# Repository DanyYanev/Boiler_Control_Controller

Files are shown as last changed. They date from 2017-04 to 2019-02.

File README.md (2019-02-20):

# Boiler_Control_Controller

## Awards

Business choice award from <b>TelebidPro</b> at <b>TUES FEST</b>

## Assignment 
 
Developing an easy-to-use device for controlling complicated water-heating systems through relays, giving the end user the ability to easily manage the heating system by the provided local touchscreen display, or remotely done so by the developed mobile Android application.

## General Characteristics of the problem

The product allows the end-user to easily and quickly control the system while being very efficient on resources such as time, electricity and water and taking fault proof into consideration.
It’s especially useful when manging the heating system of a distanced house in an underpopulated location. Using this system frees you from the responsibility to go there and manually manage everything and allows you to quickly setup your heating system just in time before you arrive as if you were just there yesterday. 

## General Working Schema

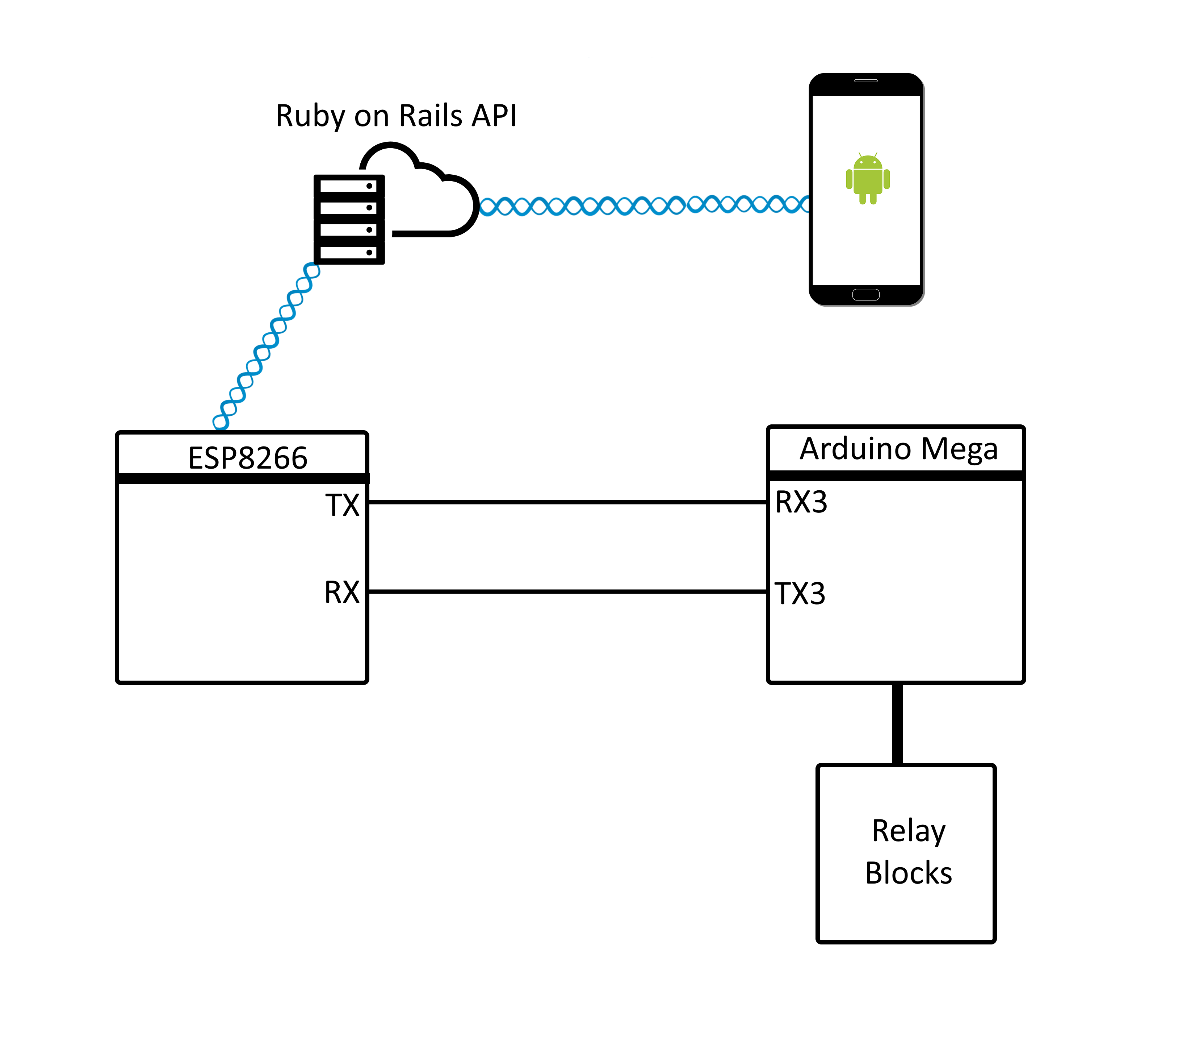
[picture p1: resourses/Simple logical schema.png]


  The whole system water-heating system is controlled by an Arduino Mega that communicates with an ESP8266 Module, the GUI is a [Nextion Display](https://nextion.itead.cc/) which is getting programmed through the Nextion Editor. All pictures were designed using Adobe Photoshop and are located in [here](/resourses/pictures/).

  The Arduino Mega and the ESP module communicate through regular serial. The serialEvent interrupt function in each controller parses the messages.

  The main functionality of the ESP module is to communicate with the API via HTTP requests. While the Mega is responsible for building the logic and managing the hardware. Both devises have acknowledgement whether or not a message has been parsed successfully.
		
  Every 10 seconds the ESP module attempts to fetch information from the server via a GET request at “[server_ulr]/users/[user_token]”. Every device has a unique user-generated user token and a controller token which is built in the ESP module and is unique for every microcontroller. After a successful request the body of the request is fetched and sent to the Mega controller. The body contains a JSON specified by the API Documentation here. If the parsing is successful the Mega controller will send an acknowledgement message. 

The ESP won’t send data to be parsed if the current running configuration is the same as the one fetched from the server.

After a local change is made the Mega will prepare a new JSON with the changes.

  Every 5 seconds if a change is made to the configuration, the updated JSON will be parsed to the ESP which will then wrap it in a PUT request and send it to the server. If an update is successful an acknowledgement message will be sent to the MEGA and the JSON object will be flushed. Else the MEGA will continue to send the updates every 5 seconds.

  All required variables for the logic to be built are saved in EEPROM. In case of power loss, on startup all variables are loaded from the local non-volatile memory.

Controller code for Boiler_Control project. ELSYS-2018

App Repo - https://github.com/DanyYanev/Boiler_Control_App

Server Repo - https://github.com/DanyYanev/Boiler_Control_Server

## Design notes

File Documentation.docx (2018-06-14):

ТЕХНОЛОГИЧНО УЧИЛИЩЕ ЕЛЕКТРОННИ СИСТЕМИ към ТЕХНИЧЕСКИ УНИВЕРСИТЕТ - СОФИЯ

# К У Р С О В П Р О Е К Т

Тема: Проектиране и реализация на контролер за отоплителна система

с GUI и Remote Access

Ученици: Даниел Янев | Научен ръководител: Инж. Росен Витанов
Денис Христов Виктор Найчев | М. Инж. Кирил Митов

СОФИЯ

2018

Assignment:

Developing an easy-to-use device for controlling complicated water-heating systems through relays, giving the end user the ability to easily manage the heating system by the provided local touchscreen display, or remotely done so by the developed mobile Android application.

GENERAL CHARACTERISTICS OF THE PROBLEM

The product allows the end-user to easily and quickly control the system while being very efficient on resources such as time, electricity and water and taking fault proof into consideration.

It’s especially useful when manging the heating system of a distanced house in an underpopulated location. Using this system frees you from the responsibility to go there and manually manage everything and allows you to quickly setup your heating system just in time before you arrive as if you were just there yesterday.

# Chapter I. Function Call Tree, Shield, Modularity, Principal Heating Schema, Memory Management, Controller communication, Libraries.

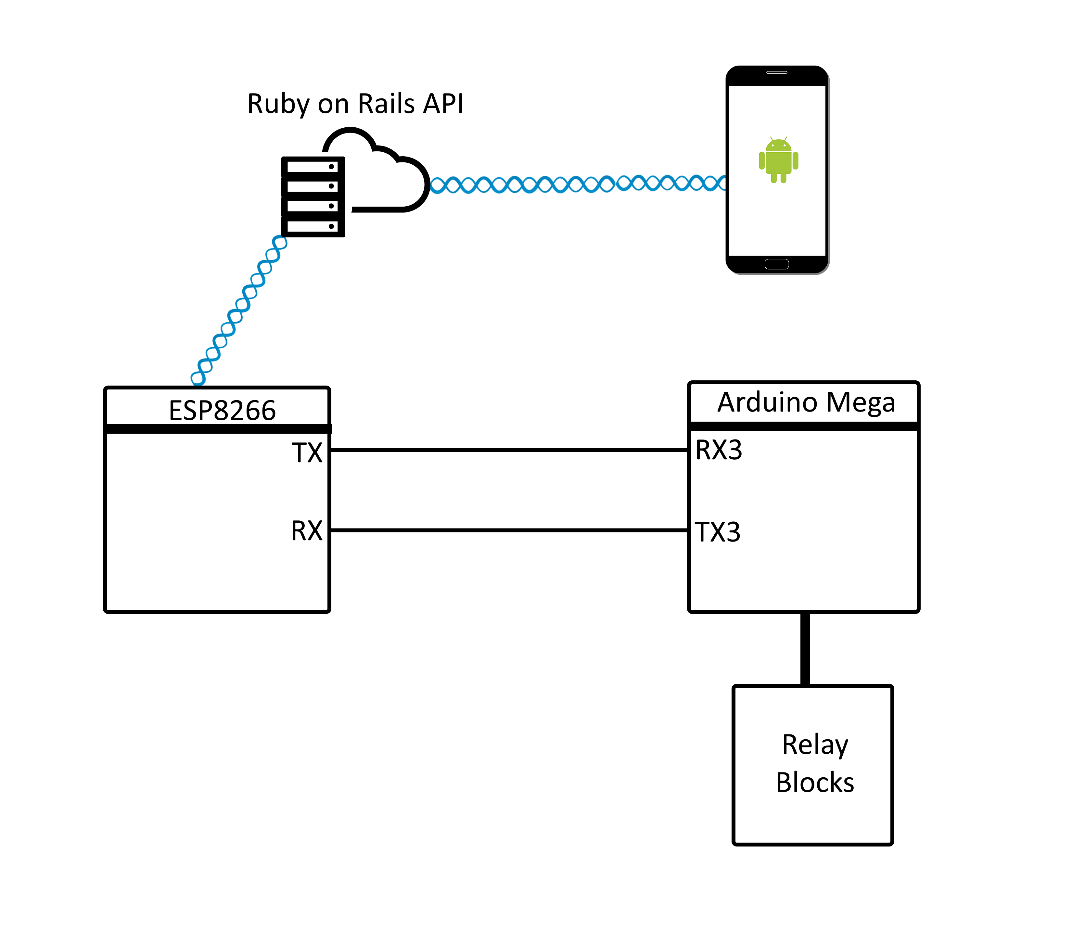
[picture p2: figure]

1. Simple Logical Scheme

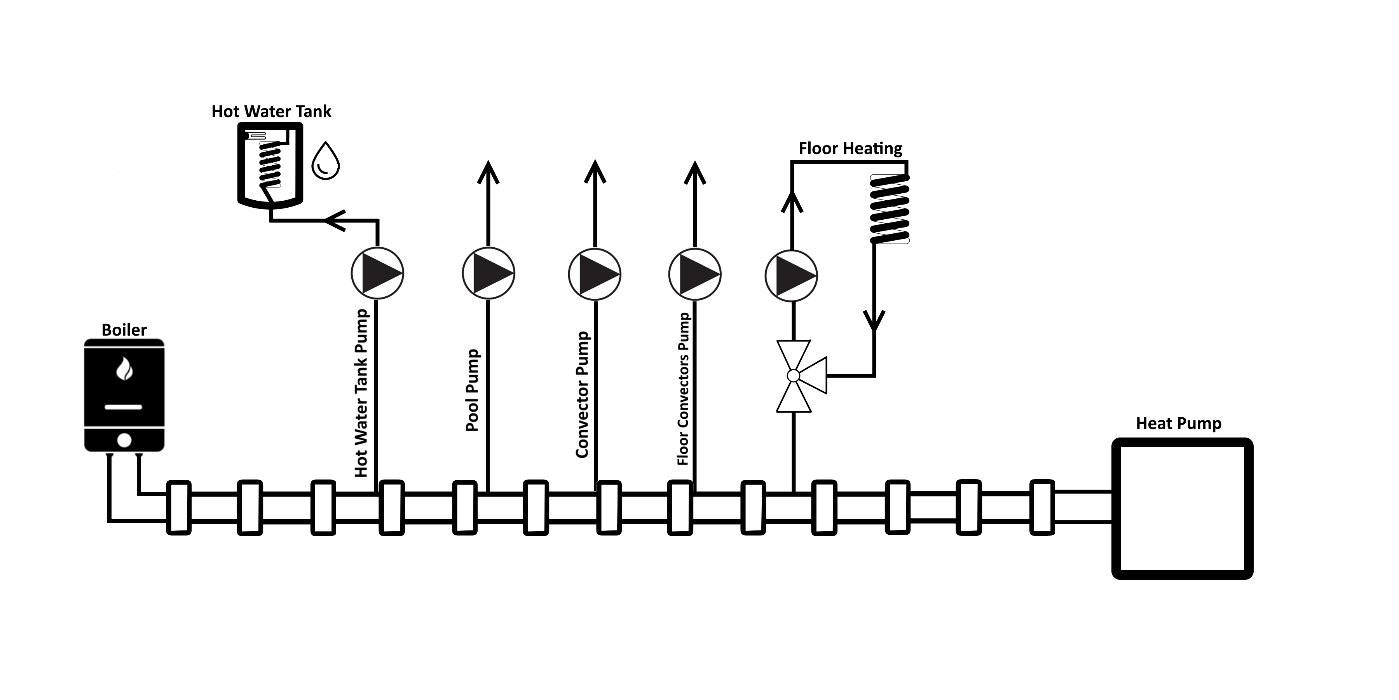
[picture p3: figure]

2. Principal Heating Schema
3. Two layer PCB Mega Shield
  a. Up to four DS18B20 Temperature Sensors
  b. One I2C Connection
  c. Power Connector
  d. Two Serial Connectors
  e. One 4 relay block connector
  f. One 8 relay block connector
  g. Two reset buttons for chip reset
  h. Option for additional ESP8266 Chip

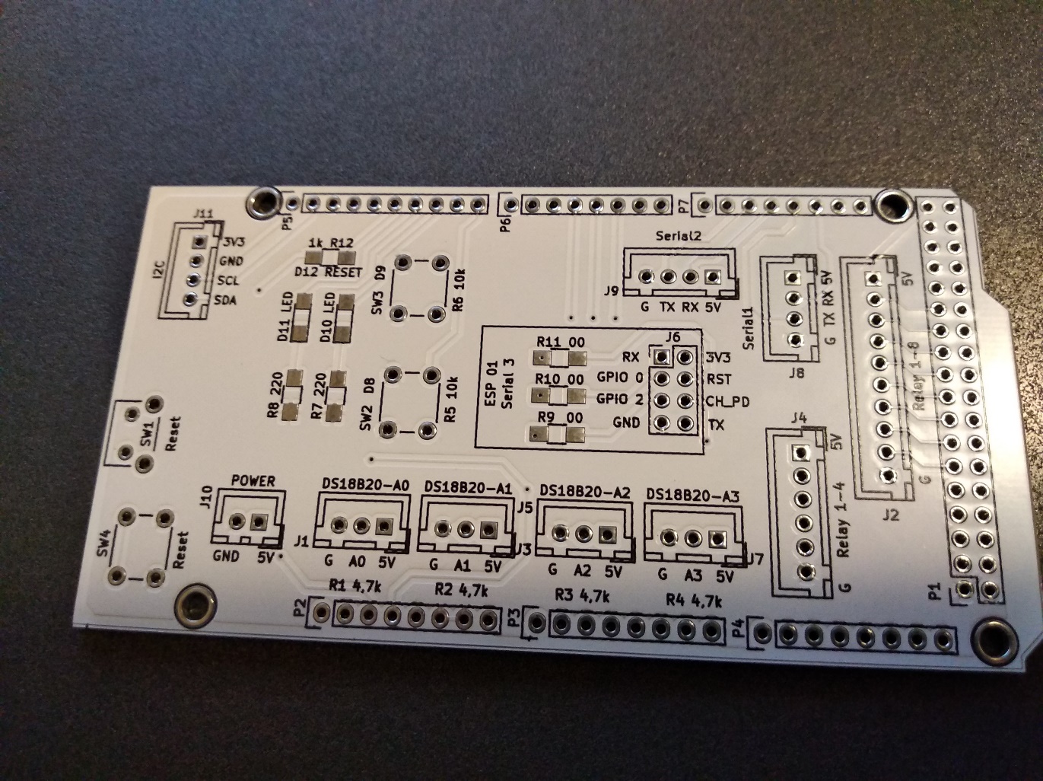
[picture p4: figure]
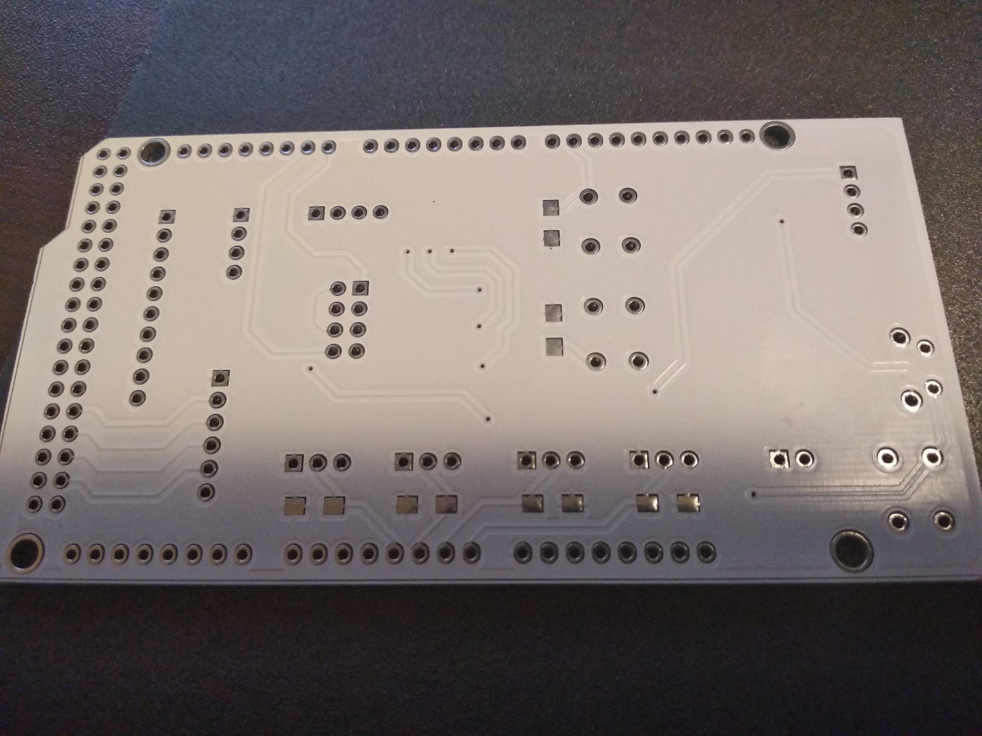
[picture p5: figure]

Front Mask

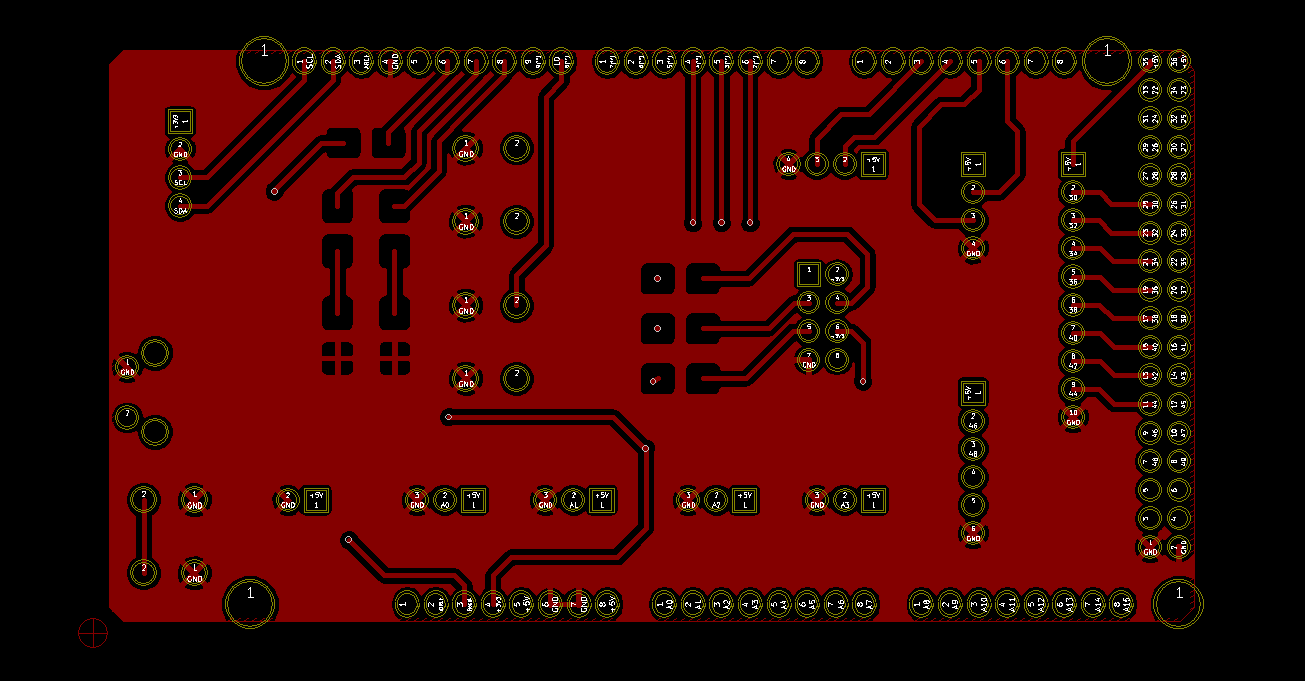
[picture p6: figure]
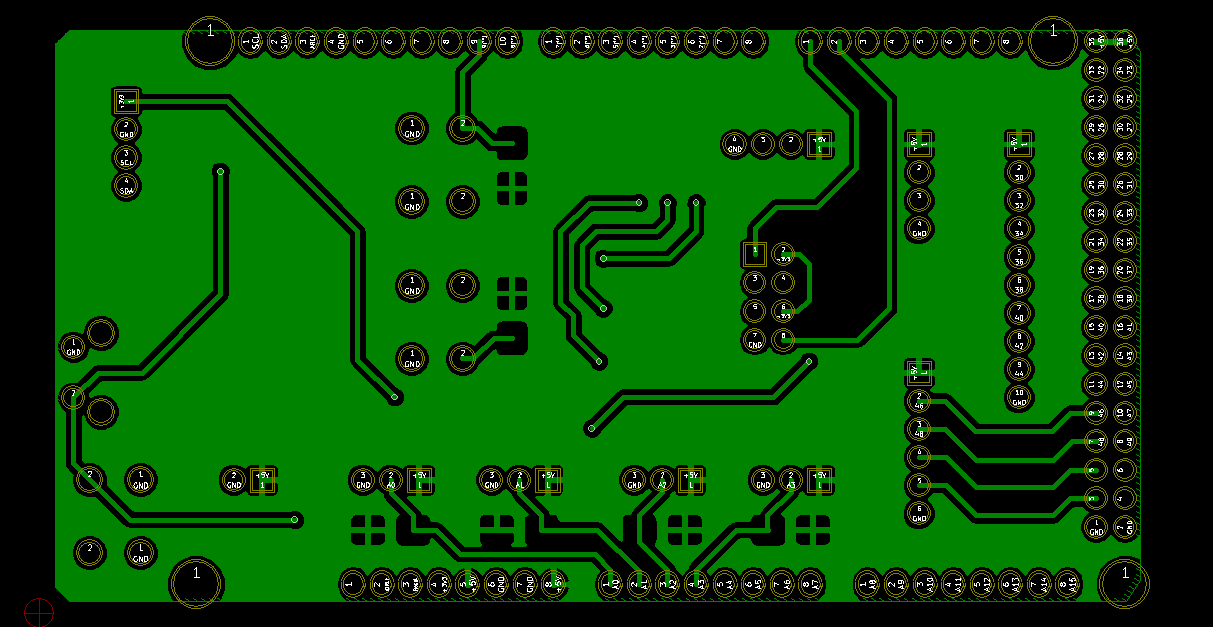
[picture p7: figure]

Back Mask

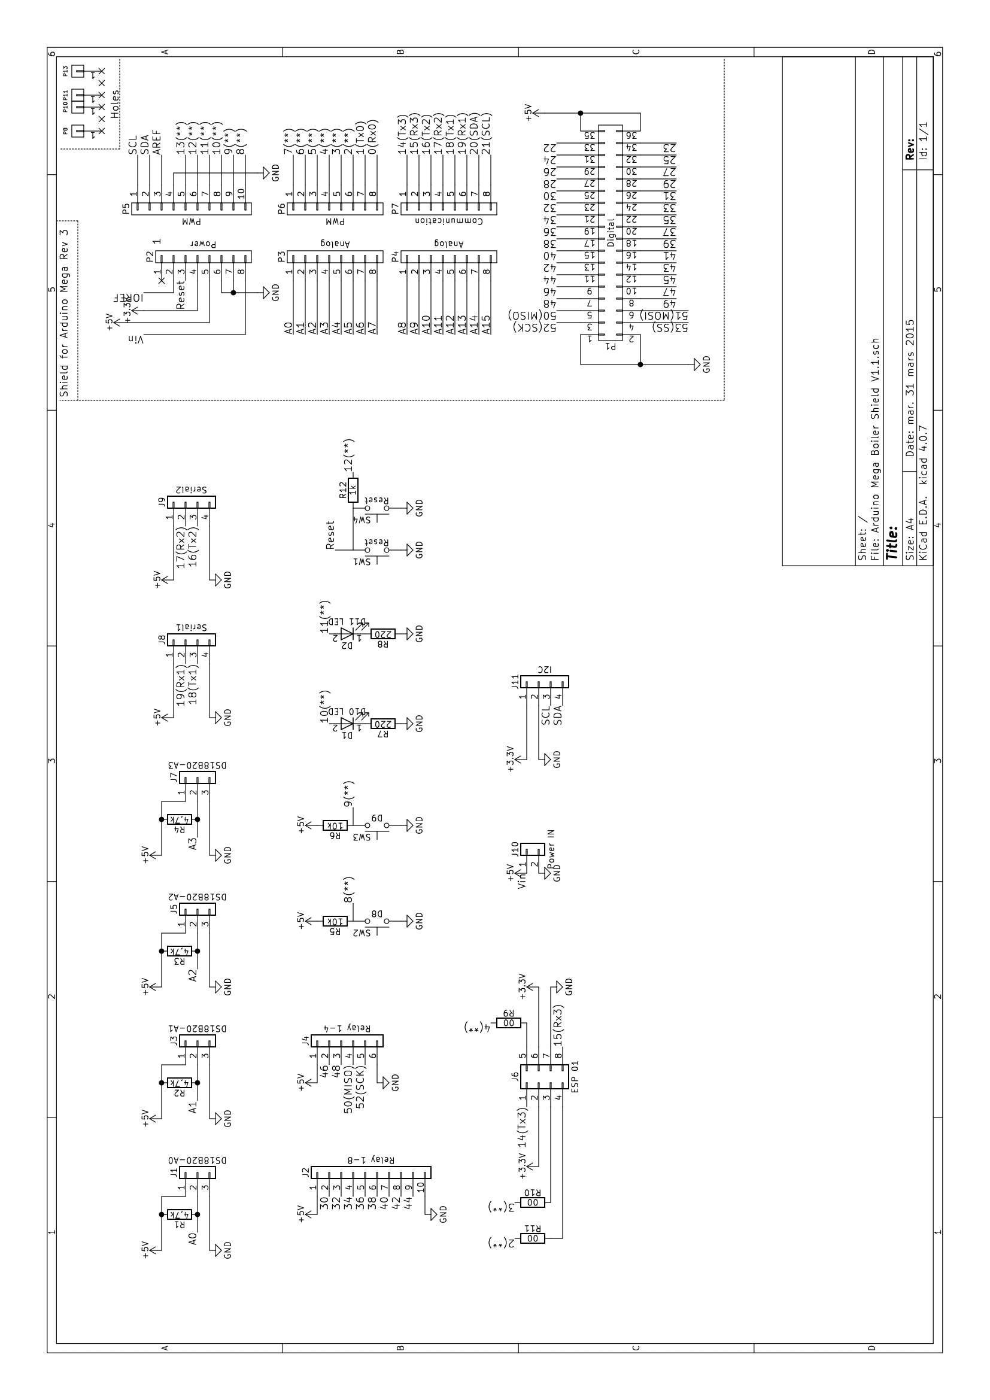
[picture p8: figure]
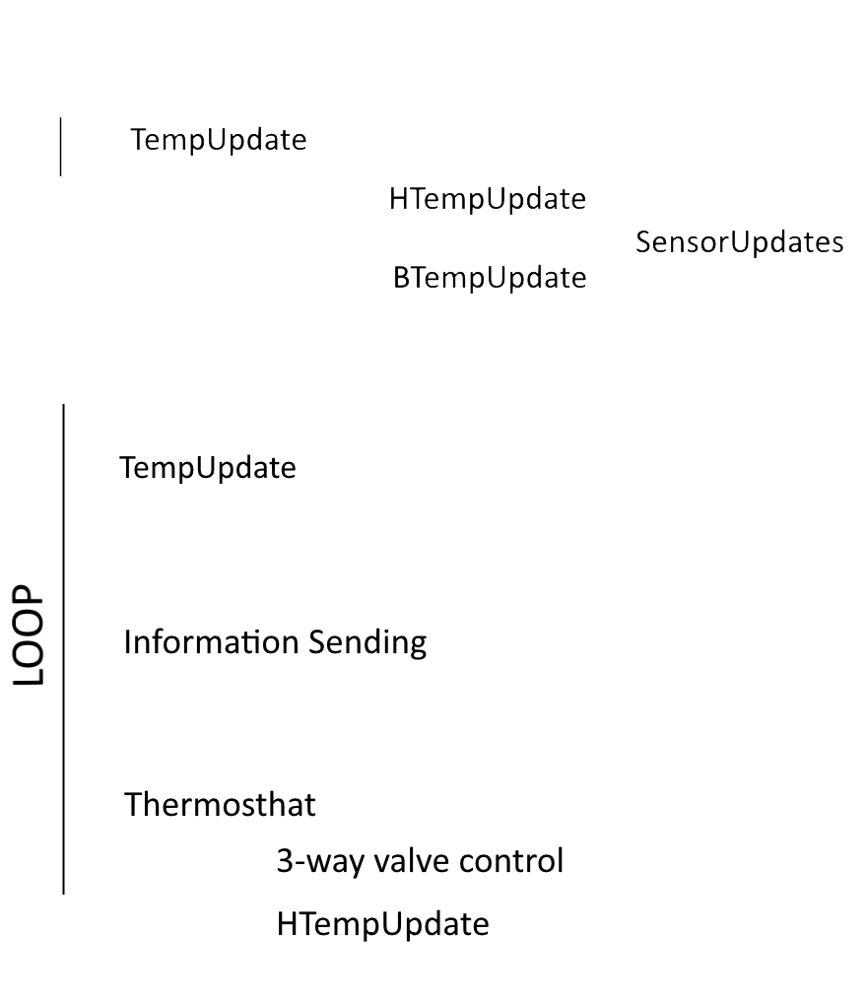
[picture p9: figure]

4. Function Call Tree

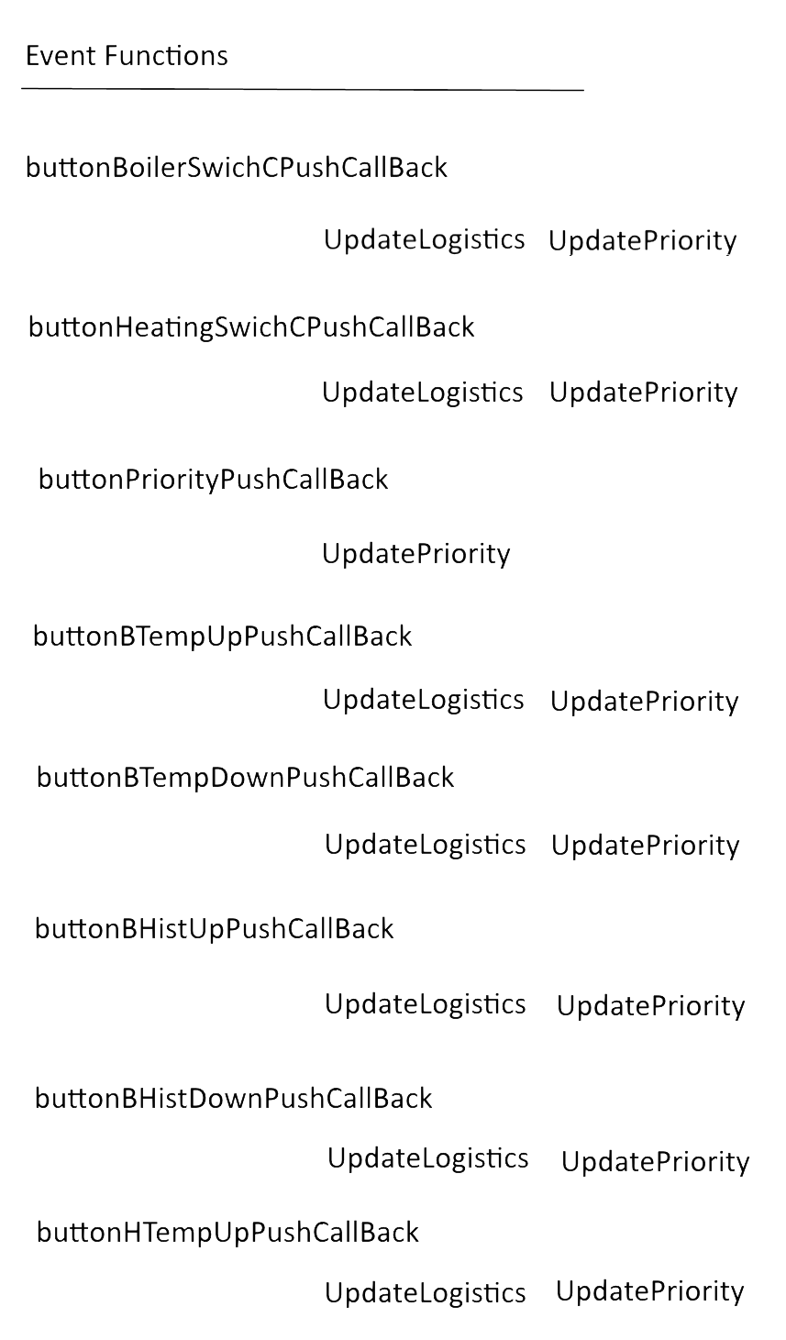
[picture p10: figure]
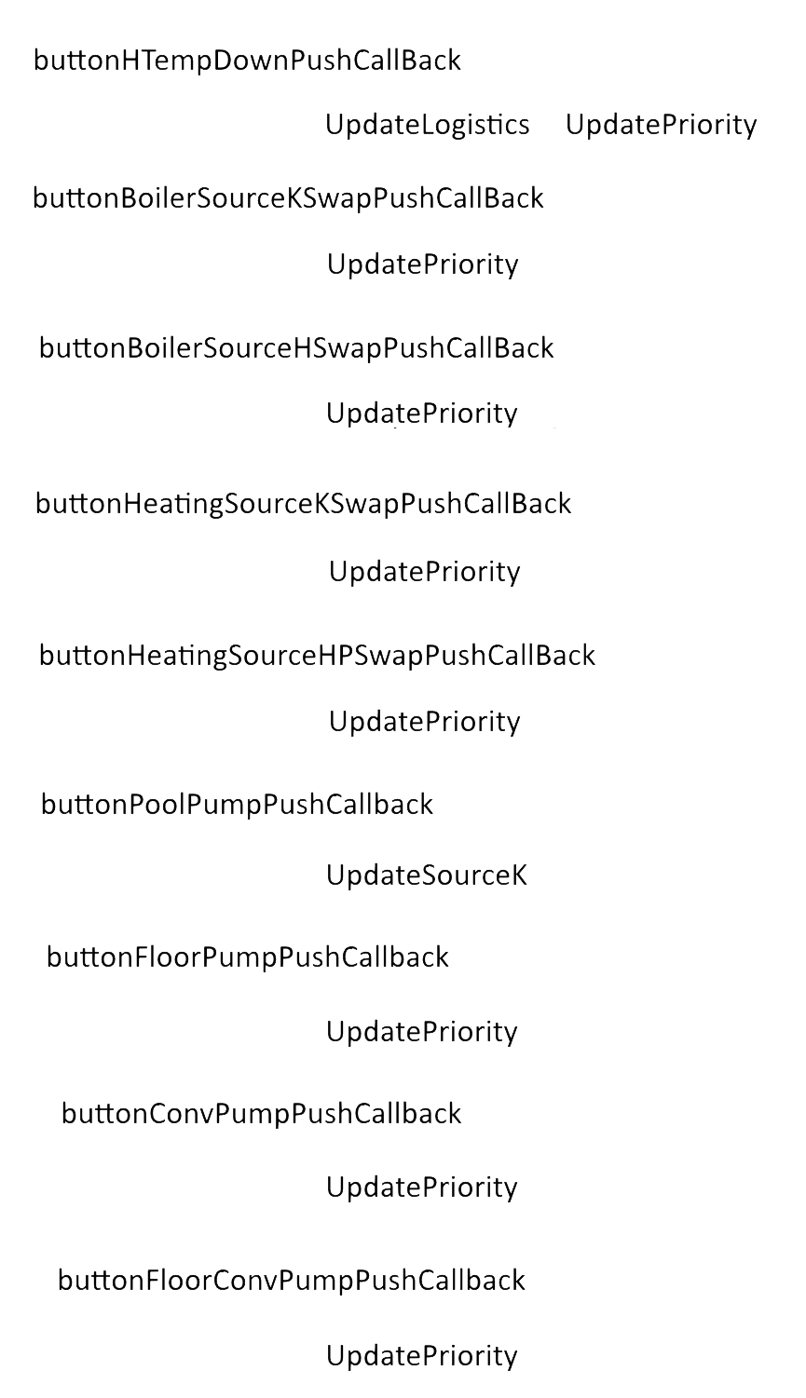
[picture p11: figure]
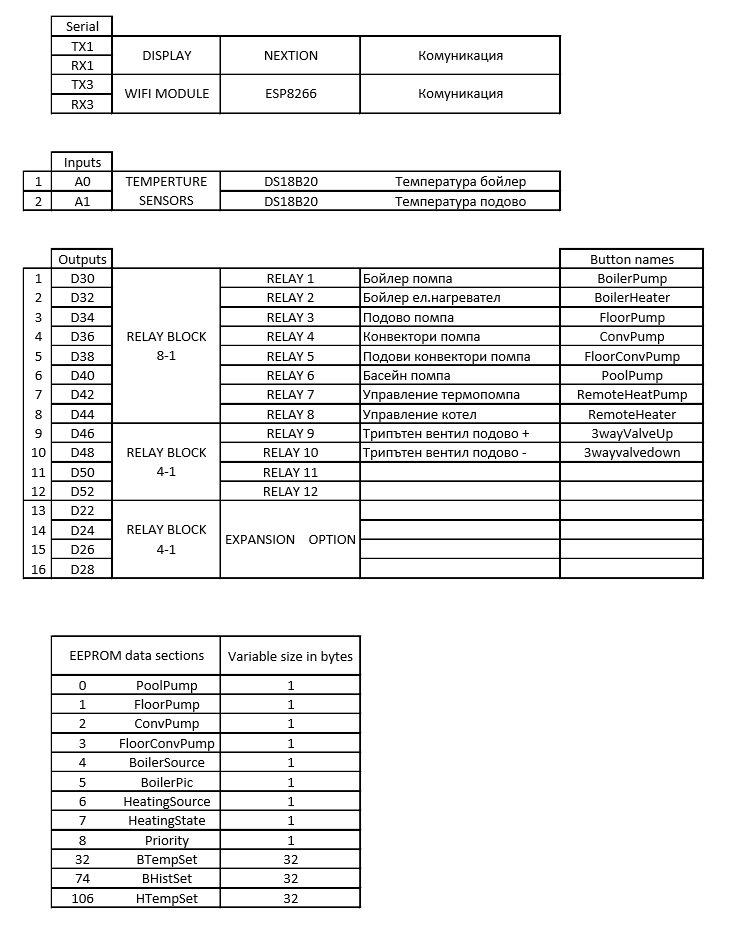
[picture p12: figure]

5. Memory and pin layout
6. Controller Communication

The Arduino Mega and the ESP module communicate through regular serial. The serialEvent interrupt function in each controller parses the messages.

The main functionality of the ESP module is to communicate with the API via HTTP requests. While the Mega is responsible for building the logic and managing the hardware. Both devises have acknowledgement whether or not a message has been parsed successfully.

Every 10 seconds the ESP module attempts to fetch information from the server via a GET request at “[server_ulr]/users/[user_token]”. Every device has a unique user-generated user token and a controller token which is built in the ESP module and is unique for every microcontroller. After a successful request the body of the request is fetched and sent to the Mega controller. The body contains a JSON specified by the API Documentation here (https://github.com/DanyYanev/Boiler_Control_Server). If the parsing is successful the Mega controller will send an acknowledgement message.

The ESP won’t send data to be parsed if the current running configuration is the same as the one fetched from the server.

After a local change is made the Mega will prepare a new JSON with the changes.

Every 5 seconds if a change is made to the configuration, the updated JSON will be parsed to the ESP which will then wrap it in a PUT request and send it to the server. If an update is successful an acknowledgement message will be sent to the MEGA and the JSON object will be flushed. Else the MEGA will continue to send the updates every 5 seconds.

All required variables for the logic to be built are saved in EEPROM. In case of power loss, on startup all variables are loaded from the local non-volatile memory.

7. Libraries used
  a. Nextion Arduino Library (https://github.com/DanyYanev/Boiler_Control_Server)
  b. Arduino JSON (https://github.com/bblanchon/ArduinoJson)
  c. OneWire (https://playground.arduino.cc/Learning/OneWire)
  d. EEPROM (https://www.arduino.cc/en/Reference/EEPROM)
  e. ESP8266 HTTP Client (https://github.com/esp8266/Arduino/tree/master/libraries/ESP8266HTTPClient)
  f. Software Serial (https://www.arduino.cc/en/Reference/softwareSerial)

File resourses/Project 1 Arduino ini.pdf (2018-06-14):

Serial
TX1
RX1
TX3
RX3

Inputs
1 | A0 | TEMPERTURE SENSORS | DS18B20 Температура бойлер
2 | A1 | | DS18B20 Температура подово
Outputs | Button names
1 2 3 4 5 6 7 8 9 10 11 12 | D30 | RELAY BLOCK 8-1 | RELAY 1 | Бойлер помпа | BoilerPump
| D32 | | RELAY 2 | Бойлер ел.нагревател | BoilerHeater
| D34 | | RELAY 3 | Подово помпа | FloorPump
| D36 | | RELAY 4 | Конвектори помпа | ConvPump
| D38 | | RELAY 5 | Подови конвектори помпа | FloorConvPump
| D40 | | RELAY 6 | Басейн помпа | PoolPump
| D42 | | RELAY 7 | Управление термопомпа | RemoteHeatPump
| D44 | | RELAY 8 | Управление котел | RemoteHeater
| D46 | RELAY BLOCK 4-1 | RELAY 9 | Трипътен вентил подово + | 3wayValveUp
| D48 | | RELAY 10 | Трипътен вентил подово - | 3wayvalvedown
| D50 | | RELAY 11
| D52 | | RELAY 12
13 | D22
14 | D24
15 | D26
16 | D28
EEPROM data sections | Variable size in bytes
0 PoolPump | 1
1 FloorPump | 1
2 ConvPump | 1
3 FloorConvPump | 1
4 BoilerSource | 1
5 BoilerPic | 1
6 HeatingSource | 1
7 HeatingState | 1
8 Priority | 1
32 BTempSet | 32
74 BHistSet | 32
106 HTempSet | 32
NEXTION | Комуникация

DISPLAY

RELAY BLOCK
4-1

EXPANSION OPTION

WIFI MODULE | ESP8266 | Комуникация

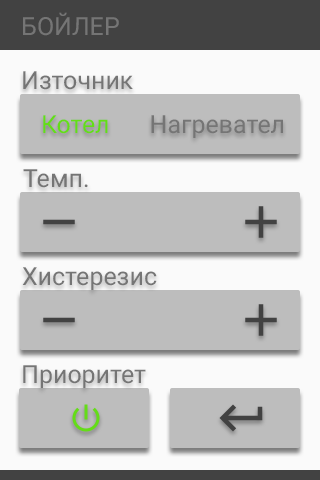
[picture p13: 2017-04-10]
resourses/pictures/Boiler page ON.png

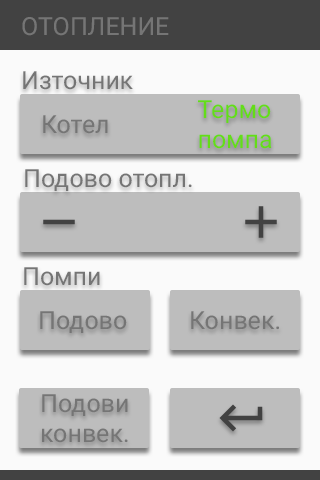
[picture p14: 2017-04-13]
resourses/pictures/Heating page OFF.png

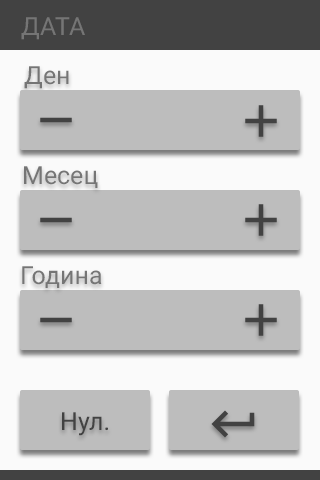
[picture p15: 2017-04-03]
resourses/pictures/Date Set page.png

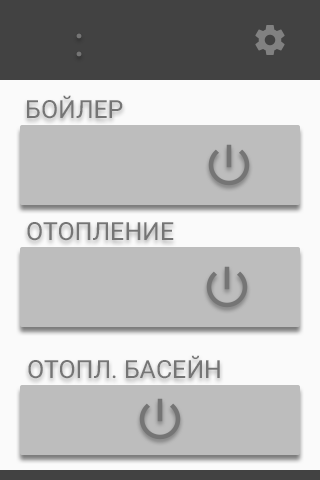
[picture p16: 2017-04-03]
resourses/pictures/Home page OFF.png

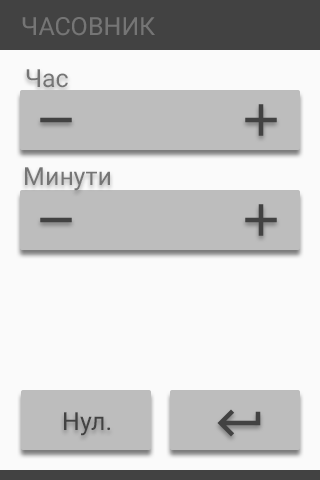
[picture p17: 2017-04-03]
resourses/pictures/Time Set page.png

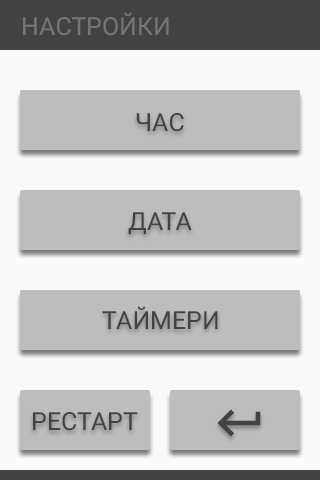
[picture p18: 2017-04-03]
resourses/pictures/Settings page.png

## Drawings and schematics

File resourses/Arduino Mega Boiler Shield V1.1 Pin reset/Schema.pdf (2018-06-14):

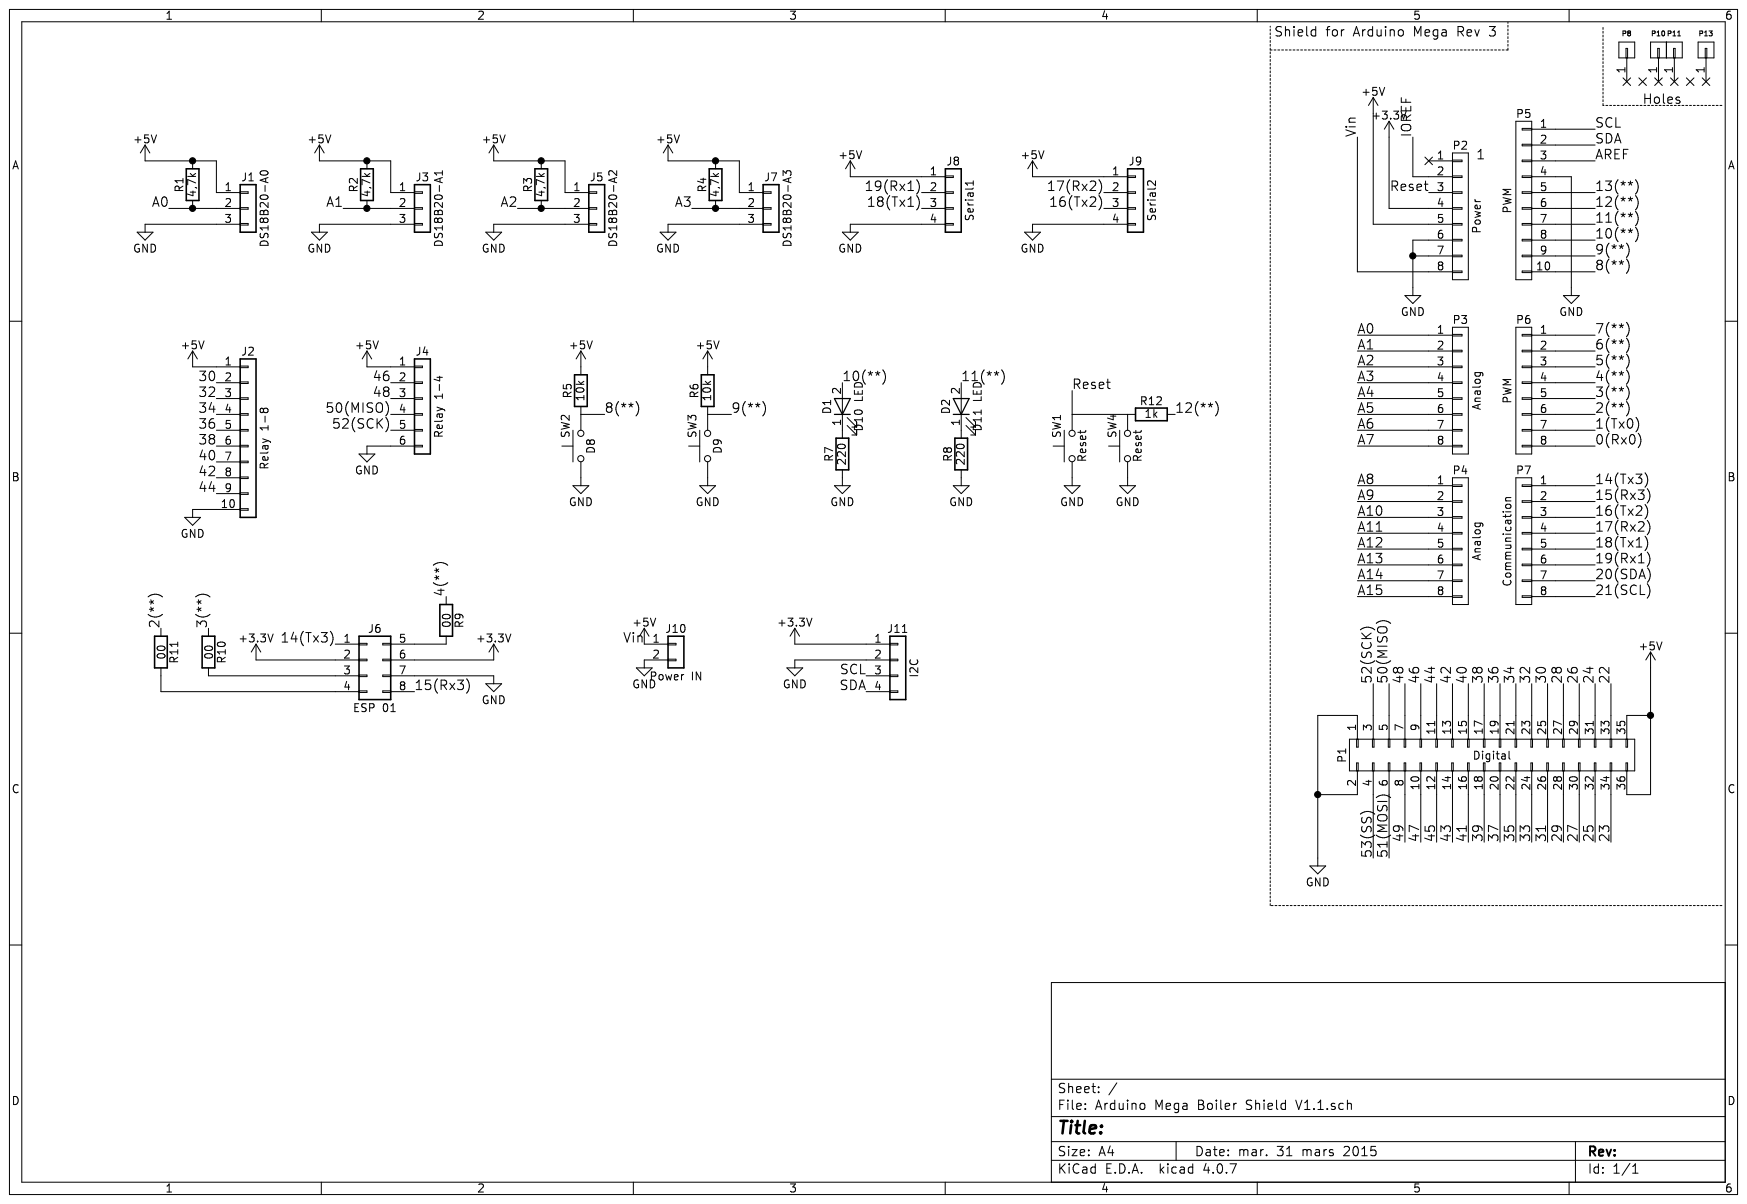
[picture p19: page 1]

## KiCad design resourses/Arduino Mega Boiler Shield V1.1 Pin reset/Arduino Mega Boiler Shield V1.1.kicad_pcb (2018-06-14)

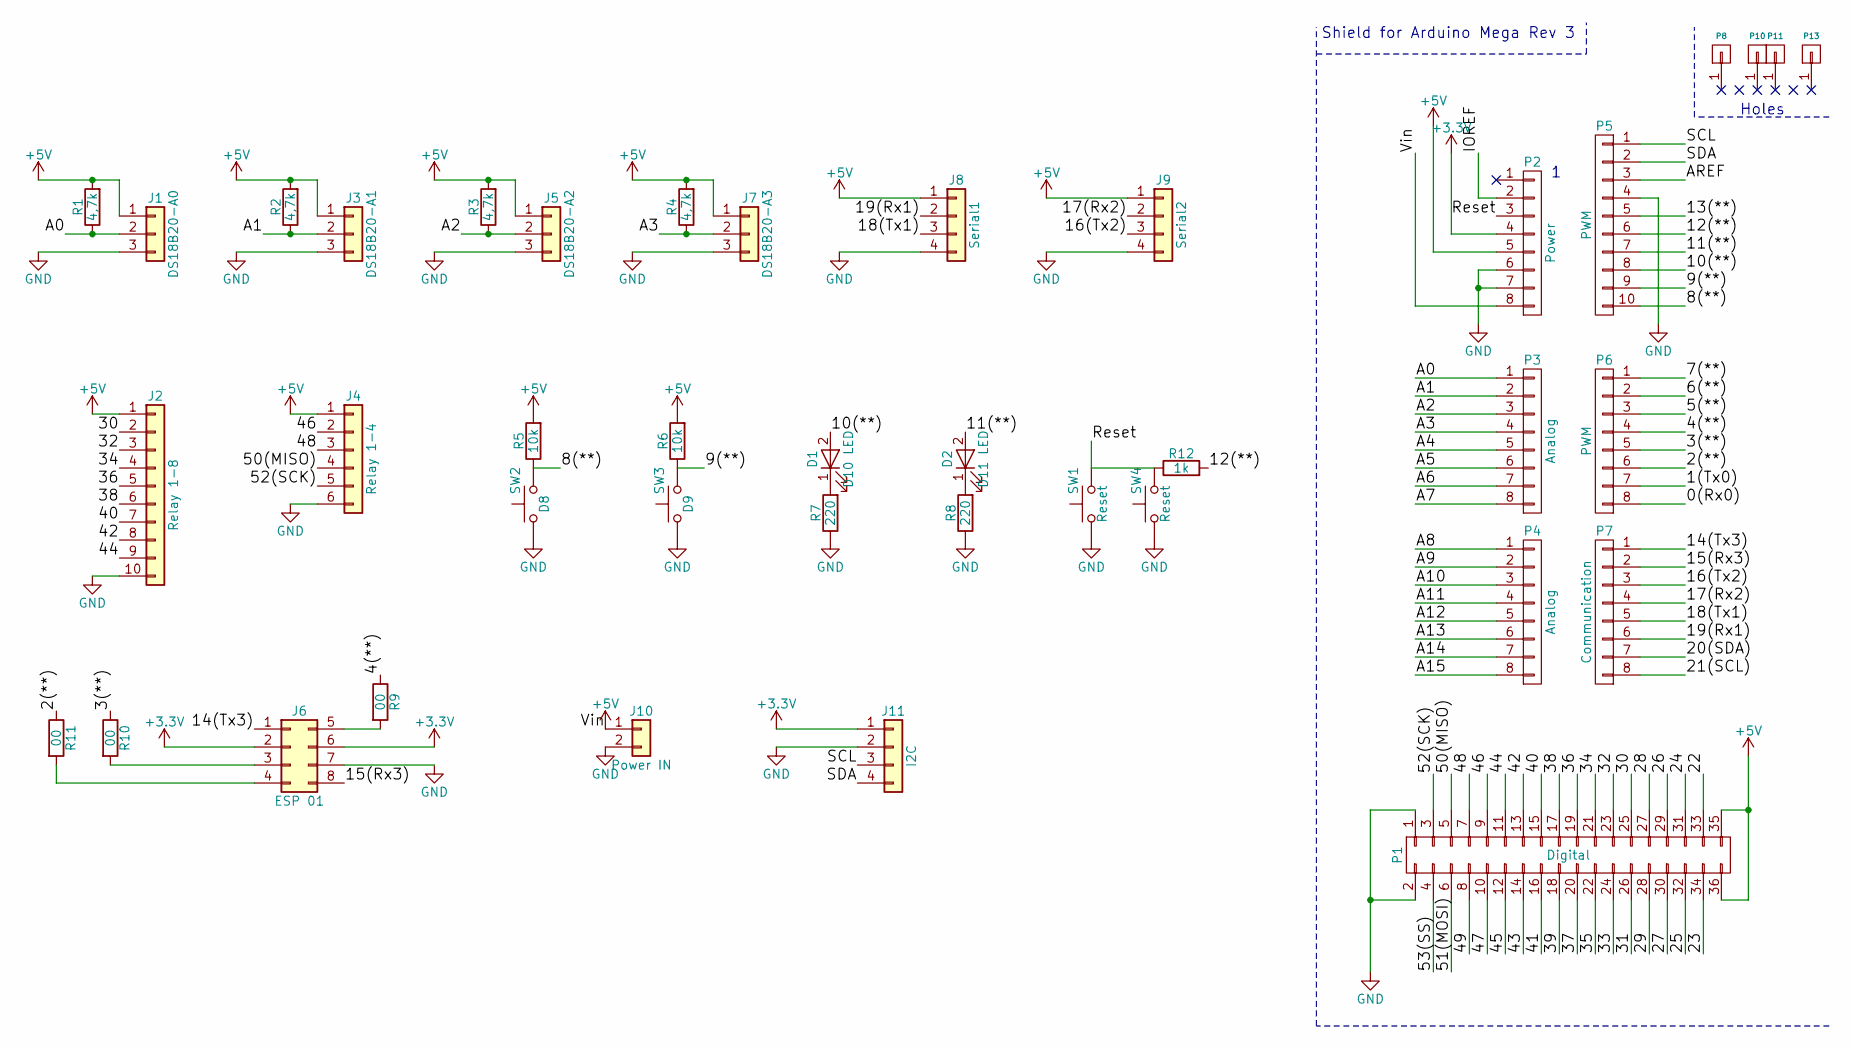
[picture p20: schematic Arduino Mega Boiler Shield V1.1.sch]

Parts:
D1: D10 LED; LED_1206_HandSoldering
D2: D11 LED; LED_1206_HandSoldering
J1: DS18B20-A0; JST_XH_B03B-XH-A_03x2.50mm_Straight
J2: Relay 1-8; JST_XH_B10B-XH-A_10x2.50mm_Straight
J3: DS18B20-A1; JST_XH_B03B-XH-A_03x2.50mm_Straight
J4: Relay 1-4; JST_XH_B06B-XH-A_06x2.50mm_Straight
J5: DS18B20-A2; JST_XH_B03B-XH-A_03x2.50mm_Straight
J6: ESP 01; Pin_Header_Straight_2x04_Pitch2.54mm
J7: DS18B20-A3; JST_XH_B03B-XH-A_03x2.50mm_Straight
J8: Serial1; JST_XH_B04B-XH-A_04x2.50mm_Straight
J9: Serial2; JST_XH_B04B-XH-A_04x2.50mm_Straight
J10: Power IN; JST_XH_B02B-XH-A_02x2.50mm_Straight
J11: I2C; JST_XH_B04B-XH-A_04x2.50mm_Straight
P1: Digital; Socket_Strip_Arduino_2x18
P2: Power; Socket_Strip_Arduino_1x08
P3, P4: Analog; Socket_Strip_Arduino_1x08
P5: PWM; Socket_Strip_Arduino_1x10
P6: PWM; Socket_Strip_Arduino_1x08
P7: Communication; Socket_Strip_Arduino_1x08
P8, P10, P11, P13: CONN_01X01; Arduino_1pin
R1, R2, R3, R4: 4,7k; R_1206_HandSoldering
R5, R6: 10k; R_1206_HandSoldering
R7, R8: 220; R_1206_HandSoldering
R9, R10, R11: 00; R_1206_HandSoldering
R12: 1k; R_1206_HandSoldering
SW1: Reset; SW_Tactile_SPST_Angled_PTS645Vx39-2LFS
SW2: D8; SW_PUSH_6mm_h5mm
SW3: D9; SW_PUSH_6mm_h5mm
SW4: Reset; SW_PUSH_6mm_h4.3mm

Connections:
+3V3: J6.2, J6.6, J11.1, P2.4
+5V: J1.1, J2.1, J3.1, J4.1, J5.1, J7.1, J8.1, J9.1, J10.1, P1.35, P1.36, P2.5, P2.8, R1.2, R2.2, R3.2, R4.2, R5.2, R6.2
/0(Rx0): P6.8
/1(Tx0): P6.7
/2(**): P6.6, R11.1
/3(**): P6.5, R10.1
/4(**): P6.4, R9.1
/5(**): P6.3
/6(**): P6.2
/7(**): P6.1
/8(**): P5.10, R5.1, SW2.2
/9(**): P5.9, R6.1, SW3.2
/10(**): D1.2 (A), P5.8
/11(**): D2.2 (A), P5.7
/12(**): P5.6, R12.2
/13(**): P5.5
/14(Tx3): J6.1, P7.1
/15(Rx3): J6.8, P7.2
/16(Tx2): J9.3, P7.3
/17(Rx2): J9.2, P7.4
/18(Tx1): J8.3, P7.5
/19(Rx1): J8.2, P7.6
/20(SDA): P7.7
/21(SCL): P7.8
/22: P1.33
/23: P1.34
/24: P1.31
/25: P1.32
/26: P1.29
/27: P1.30
/28: P1.27
/29: P1.28
/30: J2.2, P1.25
/31: P1.26
/32: J2.3, P1.23
/33: P1.24
/34: J2.4, P1.21
/35: P1.22
/36: J2.5, P1.19
/37: P1.20
/38: J2.6, P1.17
/39: P1.18
/40: J2.7, P1.15
/41: P1.16
/42: J2.8, P1.13
/43: P1.14
/44: J2.9, P1.11
/45: P1.12
/46: J4.2, P1.9
/47: P1.10
/48: J4.3, P1.7
/49: P1.8
/50(MISO): J4.4, P1.5
/51(MOSI): P1.6
/52(SCK): J4.5, P1.3
/53(SS): P1.4
/A0: J1.2, P3.1, R1.1
/A1: J3.2, P3.2, R2.1
/A2: J5.2, P3.3, R3.1
/A3: J7.2, P3.4, R4.1
/A4: P3.5
/A5: P3.6
/A6: P3.7
/A7: P3.8
/A8: P4.1
/A9: P4.2
/A10: P4.3
/A11: P4.4
/A12: P4.5
/A13: P4.6
/A14: P4.7
/A15: P4.8
/AREF: P5.3
/IOREF: P2.2
/Reset: P2.3, R12.1, SW1.2, SW4.2
/SCL: J11.3, P5.1
/SDA: J11.4, P5.2
GND: J1.3, J2.10, J3.3, J4.6, J5.3, J6.7, J7.3, J8.4, J9.4, J10.2, J11.2, P1.1, P1.2, P2.6, P2.7, P5.4, R7.1, R8.1, SW1.1, SW2.1, SW3.1, SW4.1
unnamed: D1.1 (K), R7.2
unnamed: D2.1 (K), R8.2
unnamed: J6.3, R10.2
unnamed: J6.4, R11.2
unnamed: J6.5, R9.2

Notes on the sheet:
Shield for Arduino Mega Rev 3
Holes

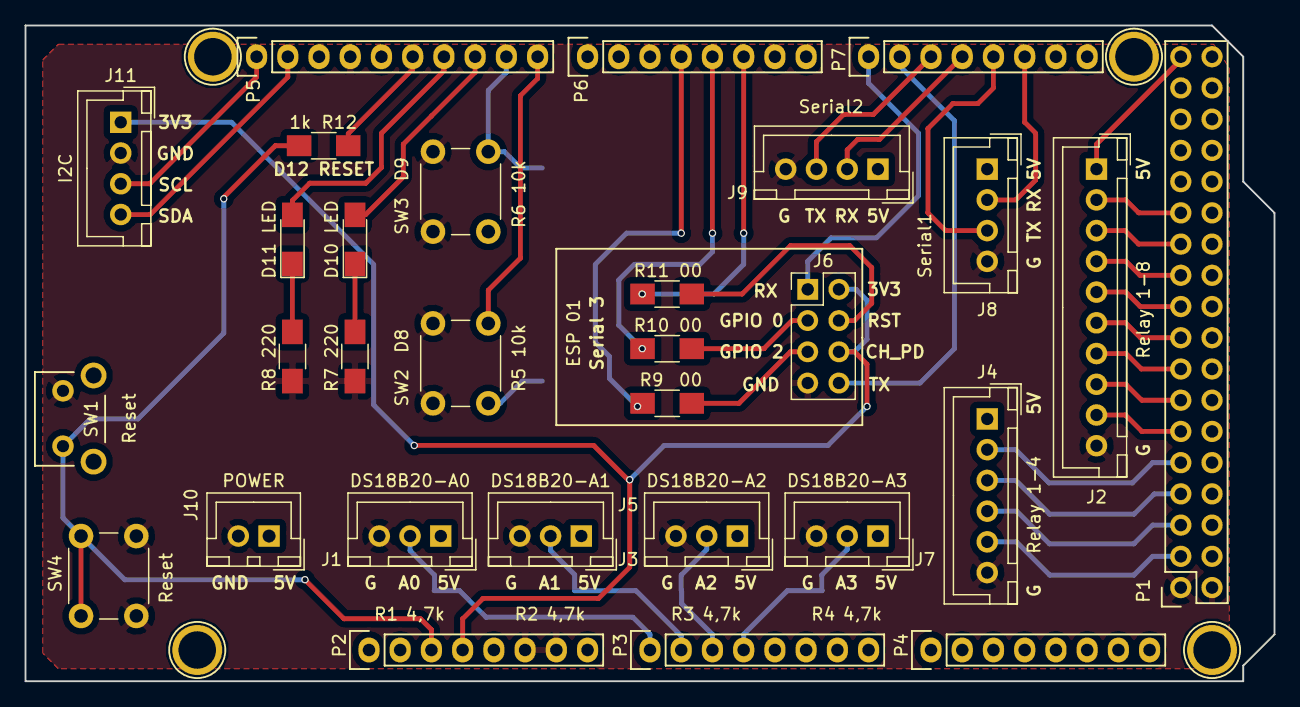
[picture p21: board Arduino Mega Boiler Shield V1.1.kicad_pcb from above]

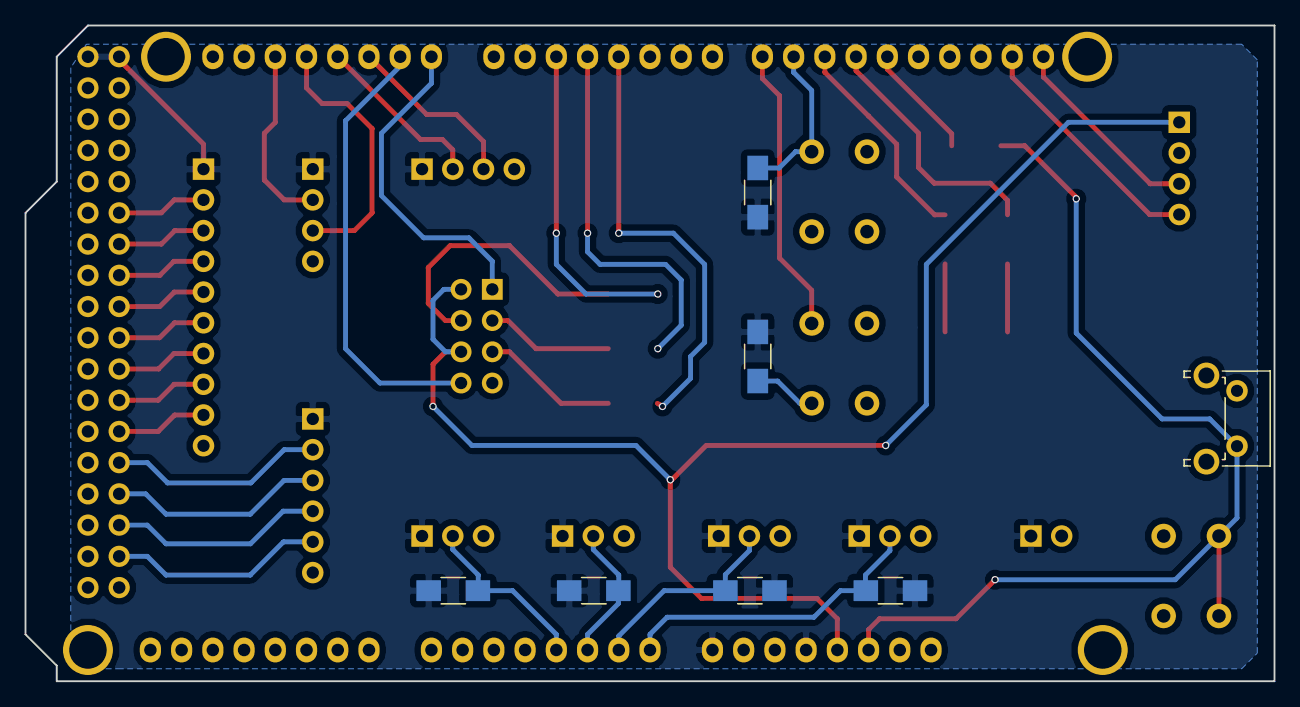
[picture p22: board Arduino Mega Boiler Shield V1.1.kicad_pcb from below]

Board: 2 copper layers, 101.6 x 53.3 mm, 40 parts (7 on the bottom side), 41 nets.

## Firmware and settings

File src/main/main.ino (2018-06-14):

#include <EEPROM.h>
//#include <doxygen.h>
#include <NexButton.h>
#include <NexCheckbox.h>
#include <NexConfig.h>
#include <NexCrop.h>
#include <NexDualStateButton.h>
#include <NexGauge.h>
#include <NexGpio.h>
#include <NexHardware.h>
#include <NexHotspot.h>
#include <NexNumber.h>
#include <NexObject.h>
#include <NexPage.h>
#include <NexPicture.h>
#include <NexProgressBar.h>
#include <NexRadio.h>
#include <NexRtc.h>
#include <NexScrolltext.h>
#include <NexSlider.h>
#include <NexText.h>
#include <NexTimer.h>
#include <Nextion.h>
#include <NexTouch.h>
#include <NexUpload.h>
#include <NexVariable.h>
#include <NexWaveform.h>
#include <OneWire.h>
#include <DallasTemperature.h>
#include <ArduinoJson.h>

#include "JsonBuilder.h"
#include "Functions_Revision3.h"
/*
 * DEFINE INPUTS/OUTPUTS 
 */
#define POOL_PUMP_EE 0
#define FLOOR_PUMP_EE 1
#define CONV_PUMP_EE 2
#define FLOOR_CONV_PUMP_EE 3
#define BOILER_SOURCE_EE 4
#define BOILER_STATE_EE 5
#define HEATING_SOURCE_EE 6
#define HEATING_STATE_EE 7
#define PRIORITY_EE 8
#define BTEMP_SET_EE 32
#define BHIST_SET_EE 74
#define HTEMP_SET_EE 106
 
int RELAY1 = 30;
int RELAY2 = 32;
int RELAY3 = 34;
int RELAY4 = 36;
int RELAY5 = 38;
int RELAY6 = 40;
int RELAY7 = 42;
int RELAY8 = 44;
int RELAY9 = 46;
int RELAY10 = 48;
int RELAY11 = 50;
int RELAY12 = 52;

int RESET_PIN = 12;

uint32_t BTemp;
uint32_t BTempSet;
uint32_t BHistSet;
uint32_t HTemp;
uint32_t HTempSet;

int HState;
int HTimeOut;

bool PoolPump;
bool FloorPump;
bool ConvPump;
bool FloorConvPump;
bool BoilerSource;
bool BoilerState;
bool BoilerPic;
bool HeatingSource;
bool HeatingState;
bool HeatingPic;
bool Priority;
bool HInMotion;
bool BCharge;

/*
 * DECLARE NEXTION objects [page id:0,component id:1, component name: "q0"]. 
 */
JsonBuilder JB("12345", "token");
 
OneWire BSensor(A0);
OneWire HSensor(A1);

DallasTemperature BSensors(&BSensor);
DallasTemperature HSensors(&HSensor);

NexPage page0 = NexPage(0, 0, "page0");
NexPage page1 = NexPage(1, 0, "page1");
NexPage page2 = NexPage(2, 0, "page2");
NexPage page5 = NexPage(5, 0, "page5");

NexNumber BTempN = NexNumber(0, 4, "BTemp");
NexNumber HTempN = NexNumber(0, 5, "HTemp");
NexNumber BTempSetN = NexNumber(1, 4, "BTempSet");
NexNumber BHistSetN = NexNumber(1, 3, "BHistSet");
NexNumber HTempSetN = NexNumber(5, 6, "HTempSet");

NexCrop buttonPoolPump = NexCrop(0, 8, "PoolPump");
NexCrop buttonBoilerSource = NexCrop(1, 10, "BSource"); // Crop on Page 1 For source pic swich
NexCrop buttonHeatingSource = NexCrop(5, 2, "HSource"); // Crop on Page 5 for source pic swich
NexCrop buttonBoilerSwichC = NexCrop(0, 9, "BoilerSwichC");
NexCrop buttonHeatingSwichC = NexCrop(0, 10, "HeatingSwichC");
NexCrop buttonPriority = NexCrop(1, 9, "Priority");
NexCrop buttonFloorPump = NexCrop(5, 9, "FloorPump");
NexCrop buttonConvPump = NexCrop(5, 10, "ConvPump");
NexCrop buttonFloorConvPump = NexCrop(5, 11, "FloorConvPump");

NexCrop buttonBTempUp = NexCrop(1, 6, "BTempUp");
NexCrop buttonBTempDown = NexCrop(1, 5, "BTempDown");
NexCrop buttonBHistUp = NexCrop(1, 8, "BHistUp");
NexCrop buttonBHistDown = NexCrop(1, 7, "BHistDown");
NexCrop buttonHTempUp = NexCrop(5, 8, "HTempUp");
NexCrop buttonHTempDown = NexCrop(5, 7, "HTempDown");

NexButton buttonBoiler = NexButton(0, 6, "BoilerM");
NexButton buttonHeating = NexButton(0, 7, "HeatingM"); 
NexButton buttonBSourceK = NexButton(1, 11, "BSourceK");
NexButton buttonBSourceH = NexButton(1, 12, "BSourceH");
NexButton buttonHSourceK = NexButton(5, 4, "HSourceK");
NexButton buttonHSourceHP = NexButton(5, 5, "HSourceHP");
NexButton buttonBackB = NexButton(1, 2, "Back");
NexButton buttonBackS = NexButton(2, 4, "Back");
NexButton buttonBackH = NexButton(5, 3, "Back");
NexButton buttonReset = NexButton(2, 5, "Reset");



/*
 * REGISTER NEXTION objects to the touch event list.
 */
NexTouch *nex_listen_list[] =
{
  &buttonBoilerSwichC,
  &buttonHeatingSwichC,
  &buttonPriority,
  &buttonBTempUp,
  &buttonBTempDown,
  &buttonBHistUp,
  &buttonBHistDown,
  &buttonHTempUp,
  &buttonHTempDown,
  &buttonPoolPump,
  &buttonFloorPump,
  &buttonConvPump,
  &buttonFloorConvPump,
  &buttonBoiler,
  &buttonHeating, 
  &buttonBSourceK,
  &buttonBSourceH,
  &buttonHSourceK,
  &buttonHSourceHP,
  &buttonBackB,
  &buttonBackS,
  &buttonBackH,
  &buttonReset,
  NULL
};

/*
   BUTTONS PAGES update function.
*/ 


void setup() {
  // put your setup code here, to run once:
   /*
   *OUTPUT setup. 
   */
 
  pinMode(RESET_PIN, OUTPUT);
  
  pinMode(RELAY1, OUTPUT);
  pinMode(RELAY2, OUTPUT);
  pinMode(RELAY3, OUTPUT);
  pinMode(RELAY4, OUTPUT);
  pinMode(RELAY5, OUTPUT);
  pinMode(RELAY6, OUTPUT);
  pinMode(RELAY7, OUTPUT);
  pinMode(RELAY8, OUTPUT);
  pinMode(RELAY9, OUTPUT);
  pinMode(RELAY10, OUTPUT);
  pinMode(RELAY11, OUTPUT);
  pinMode(RELAY12, OUTPUT);


  digitalWrite(RESET_PIN, HIGH);
   /*
   *OUTPUT start setup. 
   */
  digitalWrite(RELAY1, HIGH);
  digitalWrite(RELAY2, HIGH);
  digitalWrite(RELAY3, HIGH);
  digitalWrite(RELAY4, HIGH);
  digitalWrite(RELAY5, HIGH);
  digitalWrite(RELAY6, HIGH);
  digitalWrite(RELAY7, HIGH);
  digitalWrite(RELAY8, HIGH);
  digitalWrite(RELAY9, HIGH);
  digitalWrite(RELAY10, HIGH);
  digitalWrite(RELAY11, HIGH);
  digitalWrite(RELAY12, HIGH);
  //digitalWrite(RESET_PIN, HIGH);
  nexInit();

  EEPROM.get(BTEMP_SET_EE, BTempSet);
  EEPROM.get(BHIST_SET_EE, BHistSet);
  EEPROM.get(HTEMP_SET_EE, HTempSet);

  EEPROM.get(POOL_PUMP_EE, PoolPump);
  EEPROM.get(FLOOR_PUMP_EE, FloorPump);
  EEPROM.get(CONV_PUMP_EE, ConvPump);
  EEPROM.get(FLOOR_CONV_PUMP_EE, FloorConvPump);
  EEPROM.get(BOILER_SOURCE_EE, BoilerSource);
  EEPROM.get(BOILER_STATE_EE, BoilerPic);
  EEPROM.get(HEATING_SOURCE_EE, HeatingSource);
  EEPROM.get(HEATING_STATE_EE, HeatingPic);
  EEPROM.get(PRIORITY_EE, Priority);

  BCharge = 0;
  HTimeOut = 0;
  HInMotion = 0;

  Serial.begin(115200);
  Serial3.begin(9600);
  BSensors.begin();
  HSensors.begin();

  Serial.println("Serial start");

  /*
   *Register the pop event callback function of the current component. 
   */
  buttonBoilerSwichC.attachPush(buttonBoilerSwichCPushCallBack);
  buttonHeatingSwichC.attachPush(buttonHeatingSwichCPushCallBack);
  buttonPriority.attachPush(buttonPriorityPushCallBack);
  buttonBTempUp.attachPush(buttonBTempUpPushCallBack);
  buttonBTempDown.attachPush(buttonBTempDownPushCallBack);
  buttonBHistUp.attachPush(buttonBHistUpPushCallBack);
  buttonBHistDown.attachPush(buttonBHistDownPushCallBack);
  buttonHTempUp.attachPush(buttonHTempUpPushCallBack);
  buttonHTempDown.attachPush(buttonHTempDownPushCallBack);
    
  buttonPoolPump.attachPush(buttonPoolPumpPushCallback);
  buttonFloorPump.attachPush(buttonFloorPumpPushCallback);
  buttonConvPump.attachPush(buttonConvPumpPushCallback);
  buttonFloorConvPump.attachPush(buttonFloorConvPumpPushCallback);
  
  buttonBoiler.attachPush(buttonBoilerPushCallback);
  buttonHeating.attachPush(buttonHeatingPushCallback);
  
  buttonBSourceK.attachPush(buttonBoilerSourceKSwapPushCallBack);
  buttonBSourceH.attachPush(buttonBoilerSourceHSwapPushCallBack);
  
  buttonHSourceK.attachPush(buttonHeatingSourceKSwapPushCallBack);
  buttonHSourceHP.attachPush(buttonHeatingSourceHPSwapPushCallBack);
  
  buttonBackB.attachPush(buttonBack0PushCallback);
  buttonBackS.attachPush(buttonBack0PushCallback);
  buttonBackH.attachPush(buttonBack0PushCallback);
  buttonReset.attachPush(buttonResetPushCallback); 
  
  Serial.println("Setup done");
  //TempUpdate();
  buttonBack0PushCallback(NULL); //TempUpdate inside
  
}

unsigned long currentMillis = millis();
unsigned long lastBoilerMillis = currentMillis;
unsigned long lastHeatingMillis = currentMillis;
unsigned long lastJBMillis = currentMillis;


void loop() {

  currentMillis = millis();

  if ((unsigned long)(currentMillis - lastBoilerMillis) >= 60000) { //every minute 60000 = 60s
    TempUpdate();

    lastBoilerMillis = currentMillis;
  }

  if ((unsigned long)(currentMillis - lastJBMillis) >= 5000) {
    if(JB.getAlternated()){
      Serial3.println(JB.getJson());
    }

    lastJBMillis = currentMillis;
  }


  if ((unsigned long)(currentMillis - lastHeatingMillis) >= 3000) {
    Thermosthat();

    lastHeatingMillis = currentMillis;
  }

  nexLoop(nex_listen_list);

}

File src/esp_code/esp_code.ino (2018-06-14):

#include <ESP8266WiFi.h>
#include <ESP8266HTTPClient.h>

#include <ESP8266WebServer.h>
#include <DNSServer.h>
#include <WiFiManager.h>
#include <FS.h>

#include <ArduinoJson.h>

#define TIMEOUT_ 10000
int lastCheck = 0;

String server_ip;

const int TRIGGER_PIN = D3;

const char* CONFIG_FILE = "/config.json";

bool readConfigFile();
bool writeConfigFile();
 
void setup () {
  Serial.begin(115200);

  pinMode(TRIGGER_PIN, INPUT_PULLUP);

  if(SPIFFS.begin()){
    Serial.println("Filesystem Mounted");
  } else {
    Serial.println("Failesystem Not Mounted");
  }
  
  if (!readConfigFile()) {
    Serial.println("Failed to read configuration file, using default values");
  } else {
    WiFi.printDiag(Serial);
    WiFi.mode(WIFI_STA); 
    unsigned long startedAt = millis();
    Serial.print("After waiting ");
    int connRes = WiFi.waitForConnectResult();
    float waited = (millis()- startedAt);
    Serial.print(waited/1000);
    Serial.print(" secs in setup() connection result is ");
    Serial.println(connRes);
  }

  if (WiFi.status()!=WL_CONNECTED){
    Serial.println("Failed to connect, finishing setup anyway");
  } else{
    Serial.print("Local ip: ");
    Serial.println(WiFi.localIP());
  }
 
}
 
void loop() {
 if ( (digitalRead(TRIGGER_PIN) == LOW)) {
//  if(1){
    Serial.println("Configuration portal requested");
    
    char convertedValue[4];
    
    WiFiManagerParameter p_server_ip("server_ip", "Server IP", "", 40);

    WiFiManager wifiManager;
    
    
    wifiManager.addParameter(&p_server_ip);

    if (!wifiManager.startConfigPortal()) {
      Serial.println("Not connected to WiFi but continuing anyway.");
    } else {
      Serial.println("Connected...yeey :)");
    }
    
    server_ip = String(p_server_ip.getValue());
    
    writeConfigFile();

    ESP.reset();
    
    delay(5000);
  } else if (WiFi.status() == WL_CONNECTED && (millis() - lastCheck > TIMEOUT_)) { //Check WiFi connection status
 
    HTTPClient http;  //Declare an object of class HTTPClient

    String addr = String("http://") + String("192.168.34.157") + String(":3000/users/12345.json");
    Serial.println("SENDING TO:" + addr);
 
    http.begin(addr);  //Specify request destination
    http.addHeader("Content-Type", "application/json");
    int httpCode = http.GET();                                                                  //Send the request
 
    if (httpCode > 0) { //Check the returning code
 
      String payload = http.getString();   //Get the request response payload
      payload += '\n';
      Serial.print(payload);                     //Print the response payload
 
    }
 
    http.end();   //Close connection

    lastCheck = millis();
  }
}

void serialEvent() {
//    StaticJsonBuffer<200> jsonBuffer;
//    JsonObject& root = jsonBuffer.createObject();
//
//    root["uid"] = uid;
//    root["room"] = room;
//
//    char jsonBody[100];
//    root.printTo(jsonBody, root.measureLength() + 1);
//    Serial.println(jsonBody);
//    
//    HTTPClient http;
// 
//    http.begin(server_ip);
//    http.addHeader("Content-Type", "application/json");
//    
//    int httpCode = http.POST(String(jsonBody));
//    Serial.print("HTTP request send to: ");
//    Serial.println(server_ip);
//    if (httpCode == 200) { //Check the returning code
//      Serial.println("JSON Parsed succccsessfully");
//      digitalWrite(GREEN_LED_PIN, HIGH);
//      delay(1000);
//      digitalWrite(GREEN_LED_PIN, LOW);
//    } else if(httpCode == 401){
//      Serial.println("No such database entry");
//      tone(BUZZER_PIN, 800);
//      delay(1000);
//      noTone(BUZZER_PIN);
//    }else{
//      tone(BUZZER_PIN, 800);
//      delay(500);
//      noTone(BUZZER_PIN);
//      delay(200);
//      tone(BUZZER_PIN, 800);
//      delay(500);
//      noTone(BUZZER_PIN);
//      delay(200);
//      tone(BUZZER_PIN, 800);
//      delay(500);
//      noTone(BUZZER_PIN);
//    }
// 
//    http.end();   //Close connection
//    rfid.PICC_HaltA();
//
//    // Stop encryption on PCD
//    rfid.PCD_StopCrypto1(); 
//  }
  
  while (Serial.available()) {
    String data = Serial.readString();
    if(data == "Reset"){
      Serial.println("Reseting ESP");
      ESP.reset();
    }
  }
}

bool readConfigFile() {
  File f = SPIFFS.open(CONFIG_FILE, "r");
  
  if (!f) {
    Serial.println("Configuration file not found");
    return false; 
  } else {
    
    size_t size = f.size();

    std::unique_ptr<char[]> buf(new char[size]);

   
    f.readBytes(buf.get(), size);

    f.close();

    DynamicJsonBuffer jsonBuffer;

    JsonObject& json = jsonBuffer.parseObject(buf.get());

    if (!json.success()) {
      Serial.println("JSON parseObject() failed");
      return false;
    }
    json.printTo(Serial);

    if (json.containsKey("server_ip")) {
      server_ip = (const char*)json["server_ip"];
    }
  }
  Serial.println("\nConfig file was successfully parsed");
  return true;
}

bool writeConfigFile() {
  Serial.println("Saving config file");
  DynamicJsonBuffer jsonBuffer;
  JsonObject& json = jsonBuffer.createObject();
 
  json["server_ip"] = server_ip;

  File f = SPIFFS.open(CONFIG_FILE, "w");
  if (!f) {
    Serial.println("Failed to open config file for writing");
    return false;
  }

  json.prettyPrintTo(Serial);

  json.printTo(f);
  f.close();

  Serial.println("\nConfig file was successfully saved");
  return true;
}
  

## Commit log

2017-04-10 shit got real
    [Project 1 Arduino ini.xlsx]
2017-04-11 All pumps working, awaits Main source control
    [Project 1 Arduino ini.xlsx]
2017-04-29 Finally working combined
    [Thermostatino.fzz]
2017-07-20 small changes
    [Project 1 Arduino ini.xlsx]
2017-09-19 Unit tests
    [Project 1 Arduino ini.xlsx, Thermostatino.fzz]
2017-09-19 Fixed bug, recreated lost Revision 3 Nextion file
    [Functions_Revision3.h]
2017-09-19 Major repostory reorganization
    [Documentation.xlsx]
2017-09-19 Revert "Major repostory reorganization"
    [Documentation.xlsx]
2017-09-19 Major repository reorganization
    [Project 1 Arduino ini.xlsx]
2017-09-19 mass deletion of usless files
    [Project 1 Arduino ini.xlsx, Thermostatino.fzz]
2017-09-23 Fixed bug with changed ids
    [main.ino]
2017-12-07 Fixed bug with heating state not getting remembered
    [Functions_Revision3.h, main.ino]
2017-12-08 added funciton schematics and minor code changes
2018-02-20 fixed some errors in documentation
    [Project 1 Arduino ini.xlsx]
2018-02-26 Updated excel file and changed update algorithm
    [Project 1 Arduino ini.xlsx]
2018-02-27 Updated Excell file
    [Project 1 Arduino ini.xlsx]
2018-03-02 Fixed FloorPump not beeing affected by priority
    [Functions_Revision3.h, main.ino]
2018-03-11 Added functionalty to reset button, still doenst work :)
2018-03-11 Better temperature restrictions in case an eeprom error occurs
    [Functions_Revision3.h]
2018-03-11 Reset button works
2018-03-11 Not working esp reset for some reason, got latest updates from master onto esp branch
    [Functions_Revision3.h, esp_code.ino]
2018-05-30 Fixed race conditioning between locan and cloud updates, added message transmittion and verification
    [Functions_Revision3.h, esp_code.ino, main.ino]
2018-05-30 Hot fixes and more confirmation of actions
    [Functions_Revision3.h, esp_code.ino, main.ino]
2018-06-04 Added shield, and pngs
    [Arduino Mega Boiler Shield V1.1.kicad_pcb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]
2018-06-04 Some spreadsheet changes?
    [Project 1 Arduino ini.xlsx]
